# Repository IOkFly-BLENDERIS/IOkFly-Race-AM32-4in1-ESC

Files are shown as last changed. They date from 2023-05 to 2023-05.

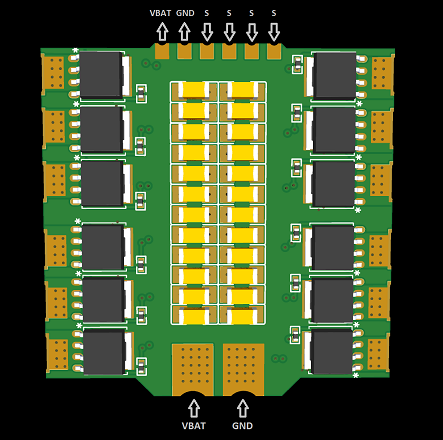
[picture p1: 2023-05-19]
Pictures/ESC pinout.png

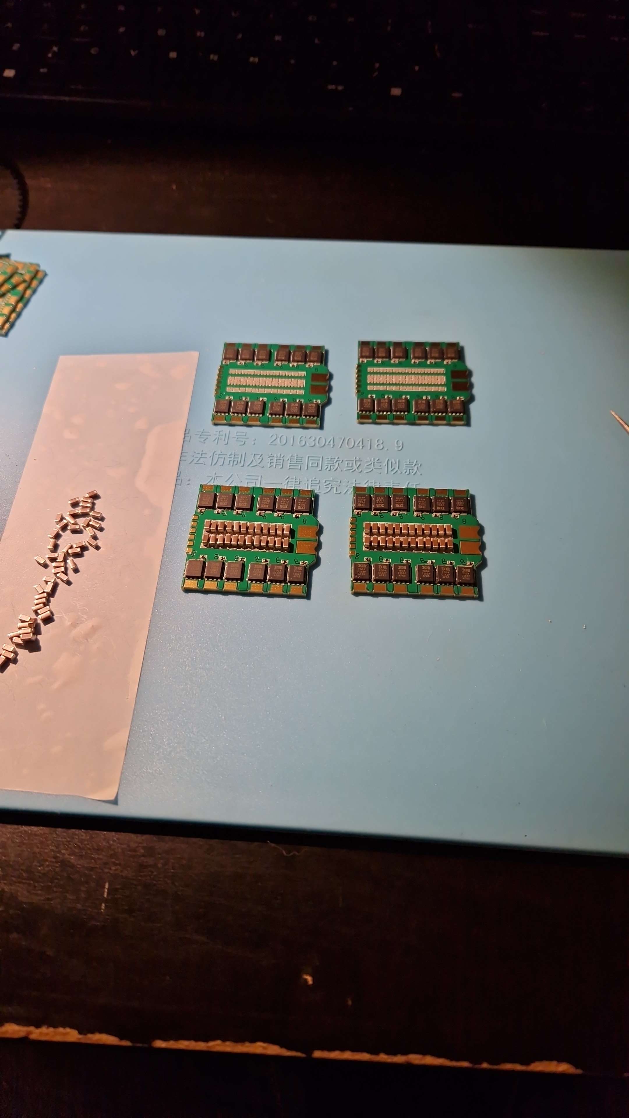
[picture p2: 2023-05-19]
Pictures/X04.jpg

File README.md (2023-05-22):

# IOkFly-Race-AM32-4in1-ESC

<p align="left">
  
</p>

4in1 ESC based on [AM32 FW](https://github.com/AlkaMotors/AM32-MultiRotor-ESC-firmware.git). Every commercial ESC on the market has some sort of design compromise to satisfy as many use cases as possible. My plan was to develop uncompromised, performance oriented ESC for quadcopter racing. Combining all the features mentioned below I believe that I achieved to design a perfect ESC for racing.

# Features

Uses AM32 open sourced 32-bit ESC FW
 * Excellent performance, excellent support and excellent community.

No mounting through holes
 * Allows for optimal mosfet layout to ensure a direct power flow path to each mosfet.
 * Mounting to frames is achieved with 3D printed customizable and replaceable brackets. Top and bottom in any combination of 20x20 or 30.5x30.5 mm.

Split board design
 * Allows to separate all logic components and traces from main power planes for optimal layout of components and somewhat reduces EMI.
 * Reduced heat buildup on sensitive logic components.
 * Allows for uncompromised power plane layers on PDB to achieve excellent power delivery performance.

2 oz copper weight on all 6 layers of power distribution board
 * Improves current flow.
 * Improves heat distribution and heat capacity.
 * Improves shock durability.

High performance Infineon mosfets.
 * In racing power deficit is not an option.
 * [IRFH7004TRPBF](https://www.infineon.com/dgdl/irfh7004pbf.pdf?fileId=5546d462533600a40153561ea3e51ed2)

No current sensor
 * Current sensor and its components use valuable board space and adds a small power flow restriction while in racing it`s almost never used. Best part is no part. There are external XT60 current sensor boards available if needed.\
Ekrānuzņēmums 2023-05-21 213739

FR4 Tg155 board material
 * Higher temperature tolerance and better manufacturing quality.

TDK low ESR filtering caps on the main voltage
 * High quality filtering capacitors reduce noise spikes on main power voltage and increase ESC longevity.

# Specification
 * Voltage: 4-6S
 * Current: 40A < ?
 * MCU - GD32E230G6U6TR
 * Gate driver - FD6288Q
 * Mosfet - IRFH7004TRPBF
 * Target: AM32_SKYSTARS_KM55_E230
 * Mounting: 30.5x30.5 or 20x20 M3 bottoms and 30.5x30.5 or 20x20 tops with M2 or M3
 * Dimensions: 38.1x38.7x12mm
 * Weight: 17g with mount

ESC pinout Processing board

# Manufacturing
I used [EasyEDA](https://easyeda.com/) (free PCB design tool) for designing the boards. [LCS](https://www.lcsc.com/) for ordering components and [JLCPCB](https://jlcpcb.com/) for manufacturing the boards as well as assembling the processing board. Processing board has a lot of 0201 components, and it is almost impossible to assemble in a DIY way.

PCB manufacturing and assembling:

PDB specification: 
 * Layers: 6
 * Base Material: FR4 Tg155
 * PCB Thickness: 1.6mm
 * Inner Copper Weight: 2oz
 * Outer Copper Weight: 2oz
 * Via Covering: Epoxy Filled & Capped
 * Surface Finish: ENIG Gold Thickness:2 U"
 * Castellated Holes: yes, Edges: 4
 
 Processing Board specification:
  * Layers: 6
  * Base Material: FR4 Tg140
  * PCB Thickness: 0.8mm
  * Inner Copper Weight: 0.5oz
  * Outer Copper Weight: 1oz
  * Via Covering: Epoxy Filled & Capped
  * Surface Finish: ENIG Gold Thickness:1 U"
  * Castellated Holes: yes, Edges: 4

For assembling the ESC, I use solder paste with stencil from JLCPCB. Alignment of Processing board on the PCB is critical as the Processing board has very tightly spaced and small castellated holes. Bad alignment may result in shorts or cold soldering. Heat gun soldering or reflow oven will require long and high heat profiles as the PCB has huge thermal capacity. I used cheap soldering heat gun on max temperature settings with medium tip and low air flow for about 5 minutes per side.\
WhatsApp attēls 2023-05-19 plkst 23 57 41 WhatsApp attēls 2023-05-19 plkst 23 58 39

# Mounting

So far, I have used only PETG material for 3D printed mounts. Works well with racing frames such as Switchback. Mounts rigidly to the frame and ESC. Bottom mount requires some sort of threaded inserts to be melted in.
\
Ekrānuzņēmums 2023-05-22 124104

Top mount takes screws directly. Top and bottom part is screwed together with M2 screws in the corners. Recommended height of the frame standoffs are 25mm.

# Testing

Flight testing:
https://www.youtube.com/watch?v=bb6y31JhEbI \
Current draw testing: Coming soon...

# Contributors

Pete Smits\
IOkFly_FluxssFPV\
AM32 Discord community

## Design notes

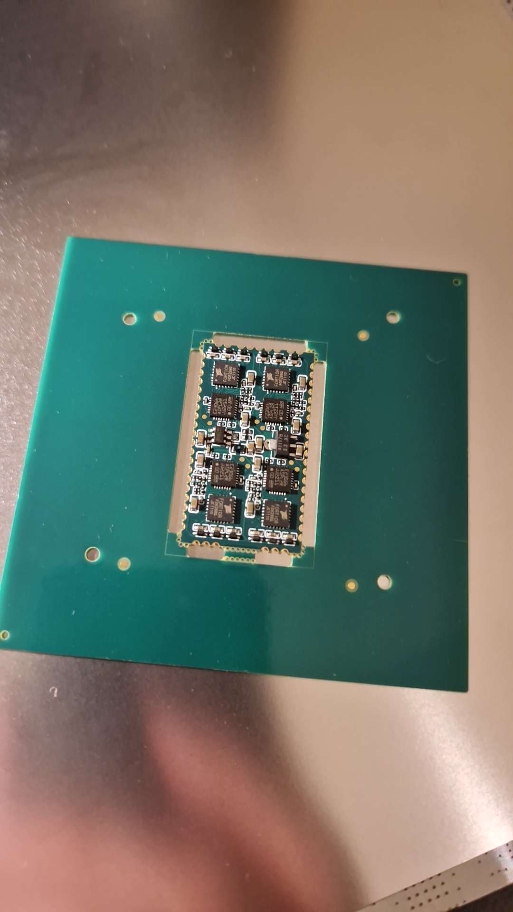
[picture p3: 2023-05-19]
Pictures/X02.jpg

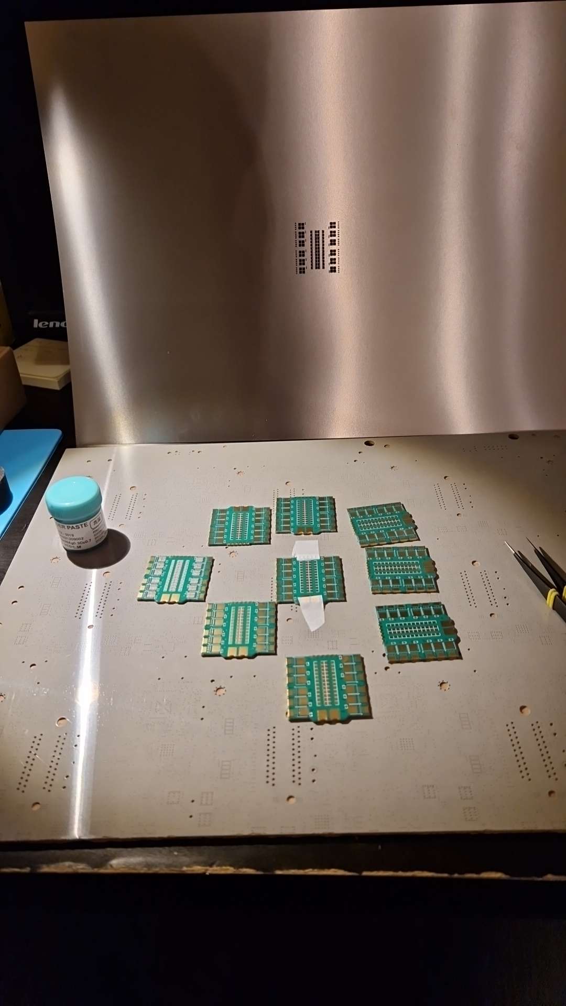
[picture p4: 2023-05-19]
Pictures/X03.jpg

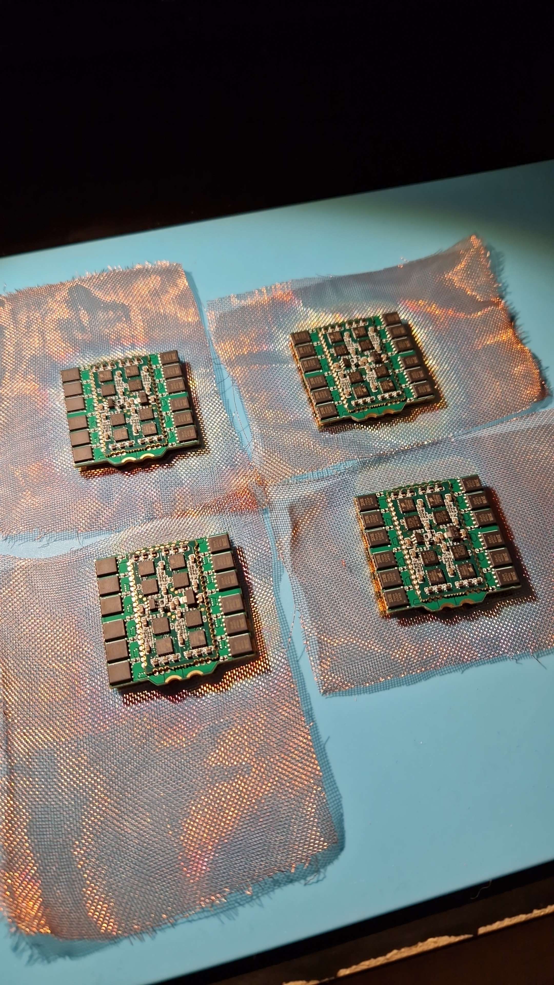
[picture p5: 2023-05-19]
Pictures/X06.jpg

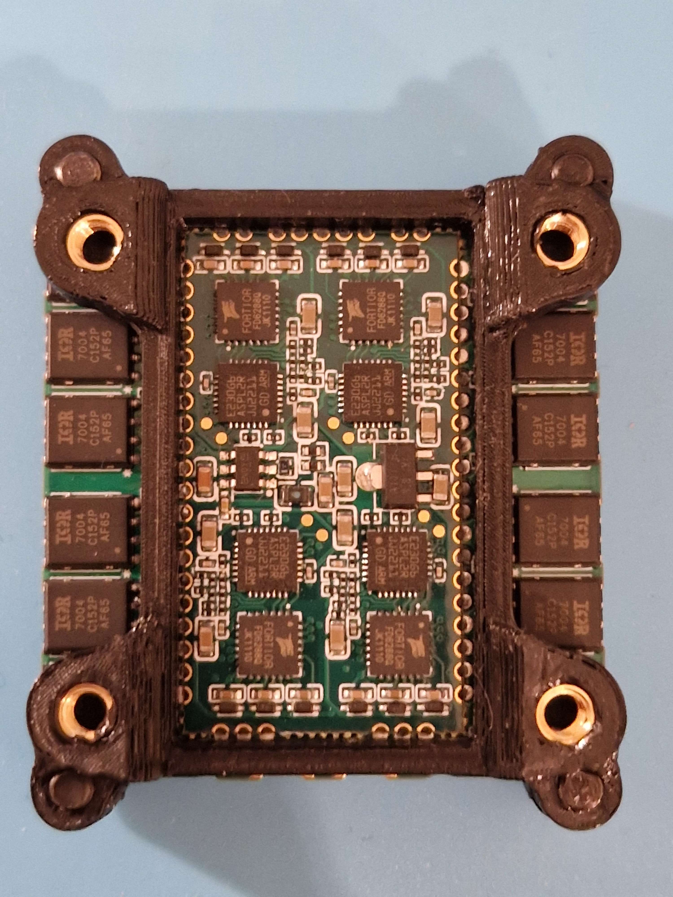
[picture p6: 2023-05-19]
Pictures/X07.jpg

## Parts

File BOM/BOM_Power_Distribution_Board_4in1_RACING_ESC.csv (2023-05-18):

ID | Name | Designator | Footprint | Quantity | Manufacturer Part | Manufacturer | Supplier | Supplier Part | Price
1 | SQJ138ELP-T1_GE3 | U1,U2,U3,U7,U8,U9,U13,U14,U15,U19,U20,U21,U4,U5,U6,U10,U11,U12,U16,U17,U18,U22,U23,U24 | POWERPAK_SO-8L_3_VIS | 24 | IRFH7004TRPBF | Infineon(英飞凌) | LCSC | C112334
2 | 20 | R1,R2,R3,R7,R8,R9,R13,R14,R15,R19,R20,R21,R10,R11,R12,R16,R17,R18,R22,R23,R24,R4,R5,R6 | R0402 | 24 | RC0402FR-0720RL | YAGEO(国巨) | LCSC | C138031 | 0.001
3 | 10uF | C1,C2,C3,C4,C5,C7,C8,C9,C10,C11,C13,C14,C15,C16,C17,C19,C20,C21,C22,C23,C25,C26,C27,C28 | C1206 | 24 | C3216X7R1V106KT000E | TDK | LCSC | C76666 | 0.245

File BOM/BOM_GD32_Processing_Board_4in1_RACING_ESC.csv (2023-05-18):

ID | Name | Designator | Footprint | Quantity | Manufacturer Part | Manufacturer | Supplier | Supplier Part | Price
1 | 1uF | C1,C2,C3,C22,C23,C24,C32,C33,C34,C37,C42,C43 | C0402 | 12 | CL05A105KO5NNNC | SAMSUNG(三星) | LCSC | C29266
2 | 10uF | C4,C9,C20,C30,C40,C45 | C0603 | 6 | CL10A106MO8NQNC | SAMSUNG(三星) | LCSC | C92487 | 0.003
3 | 100nF | C7 | C0402_NEW | 1 | CL05B104KO5NNNC | SAMSUNG(三星) | LCSC | C1525
4 | 4.32K | R52 | R0402 | 1 | RC0402FR-074K32L | YAGEO(国巨) | LCSC | C273329
5 | 1K | R1,R2,R3,R12,R13,R22,R23,R24,R25,R34,R35,R36,R37,R46,R47,R48 | R0201 | 16 | RC0201FR-071KL | YAGEO | LCSC | C138165
6 | 10kΩ | R4,R5,R6,R7,R8,R9,R10,R11,R14,R15,R16,R17,R18,R19,R20,R21,R26,R27,R28,R29,R30,R31,R32,R33,R38,R39,R40,R41,R42,R43,R44,R45 | R0201 | 32 | AR01DTD1002 | Viking Tech | LCSC | C319932 | 0.006
7 | GD32E230G6U6TR | U1,U6,U8,U10 | QFN-28_L4.0-W4.0-P0.40-BL-EP2.8 | 4 | GD32E230G6U6TR | GigaDevice(兆易创新) | LCSC | C2835081 | 0.272
8 | FD6288Q_C328453 | U2,U4,U7,U9 | QFN-24_L4.0-W4.0-P0.50-BL-EP2.6 | 4 | FD6288Q | Fortior Tech | LCSC | C328453 | 0.127
9 | 1N4148WT_C68948 | D1,D2,D3,D4,D5,D6,D7,D8,D9,D10,D11,D12 | SOD-523_L1.2-W0.8-LS1.6-RD | 12 | 1N4148WT T4 | CJ(江苏长电/长晶) | LCSC | C68948 | 0.003
10 | RB161QS-40T18R | D13 | X2-DFN1006-2_L1.0-W0.6-P0.65-RD | 1 | RB161QS-40T18R | ROHM(罗姆) | LCSC | C2837790 | 0.016
11 | 22uH | L1 | IND-SMD_L1.8-W1.2 | 1 | SLC1608F220KTT | Sunltech(韩国顺磁) | LCSC | C411912 | 0.01
12 | 49.9K | R50 | R0402 | 1 | RC0402FR-0749K9L | YAGEO(国巨) | LCSC | C137969
13 | AOZ1282CI | U11 | SOT-23-6_L2.9-W1.6-P0.95-LS2.8-BR | 1 | AOZ1282CI | AOS | LCSC | C111916 | 0.133
14 | CJA1117B-3.3 | U3 | SOT-89-3_L4.5-W2.5-P1.50-LS4.2-BR | 1 | CJA1117B-3.3 | CJ(江苏长电/长晶) | LCSC | C24253 | 0.011
15 | 22uF | C5,C13,C14,C18,C25 | C0603 | 5 | CL10A226MQ8NRNC | SAMSUNG(三星) | LCSC | C59461 | 0.001
16 | 1uF | C6,C12,C17,C27 | C0201 | 4 | CL03A105MO3NRNH | SAMSUNG(三星) | LCSC | C307385 | 0.002
17 | 1uF | C8,C10,C11,C15,C16,C19,C21,C26 | C0201 | 8 | CL03A105MQ3CSNH | SAMSUNG(三星) | LCSC | C53067
18 | 10uF | C28 | C0603 | 1 | GRM188R6YA106MA73D | muRata(村田) | LCSC | C194427 | 0.006

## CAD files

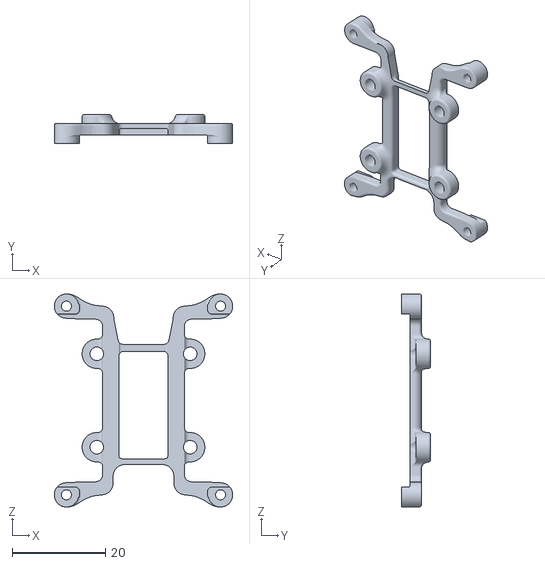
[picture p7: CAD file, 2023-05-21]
Mounting/TOP_20x20_M3.STL
38.2 x 6.30 x 45.6

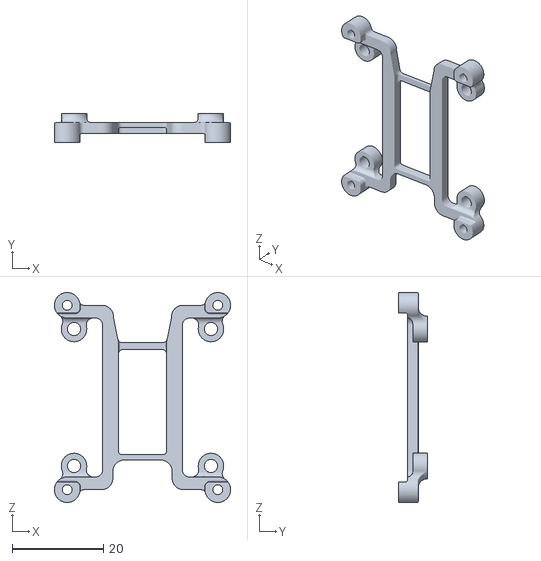
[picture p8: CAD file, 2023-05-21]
Mounting/TOP_30x30_M3.STL
38.6 x 6.30 x 46.0

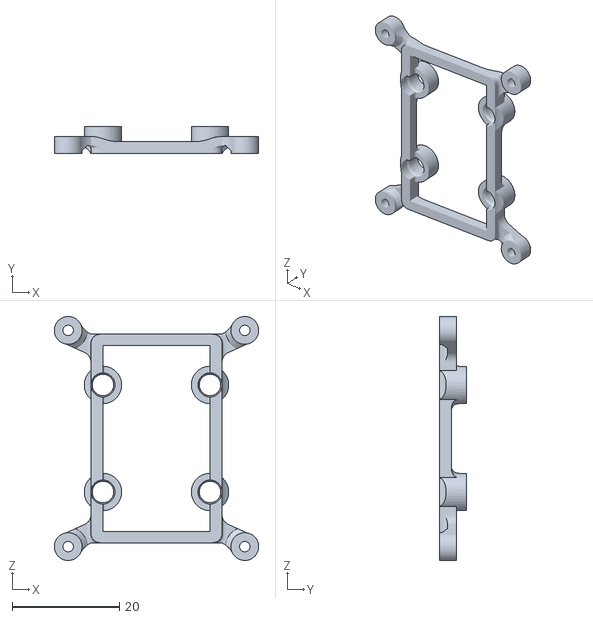
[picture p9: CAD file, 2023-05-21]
Mounting/BOTTOM_20x20_M3_Brass INSERT.STL
38.2 x 5.10 x 45.6

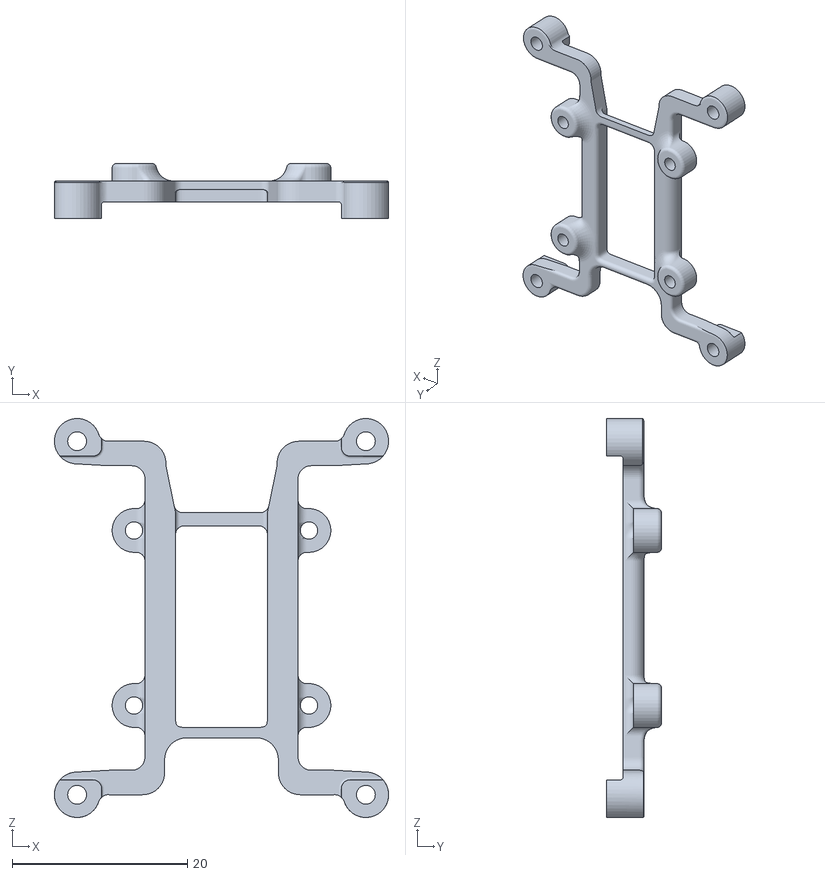
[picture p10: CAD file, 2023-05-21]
Mounting/TOP_20x20_M2.STL
38.2 x 6.30 x 45.6

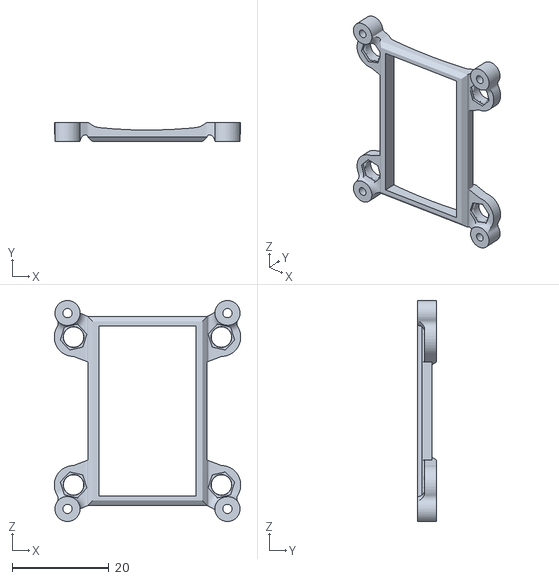
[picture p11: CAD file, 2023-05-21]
Mounting/BOTTOM_30x30_Small M3 INSERTS.STL
38.5 x 4.00 x 45.6

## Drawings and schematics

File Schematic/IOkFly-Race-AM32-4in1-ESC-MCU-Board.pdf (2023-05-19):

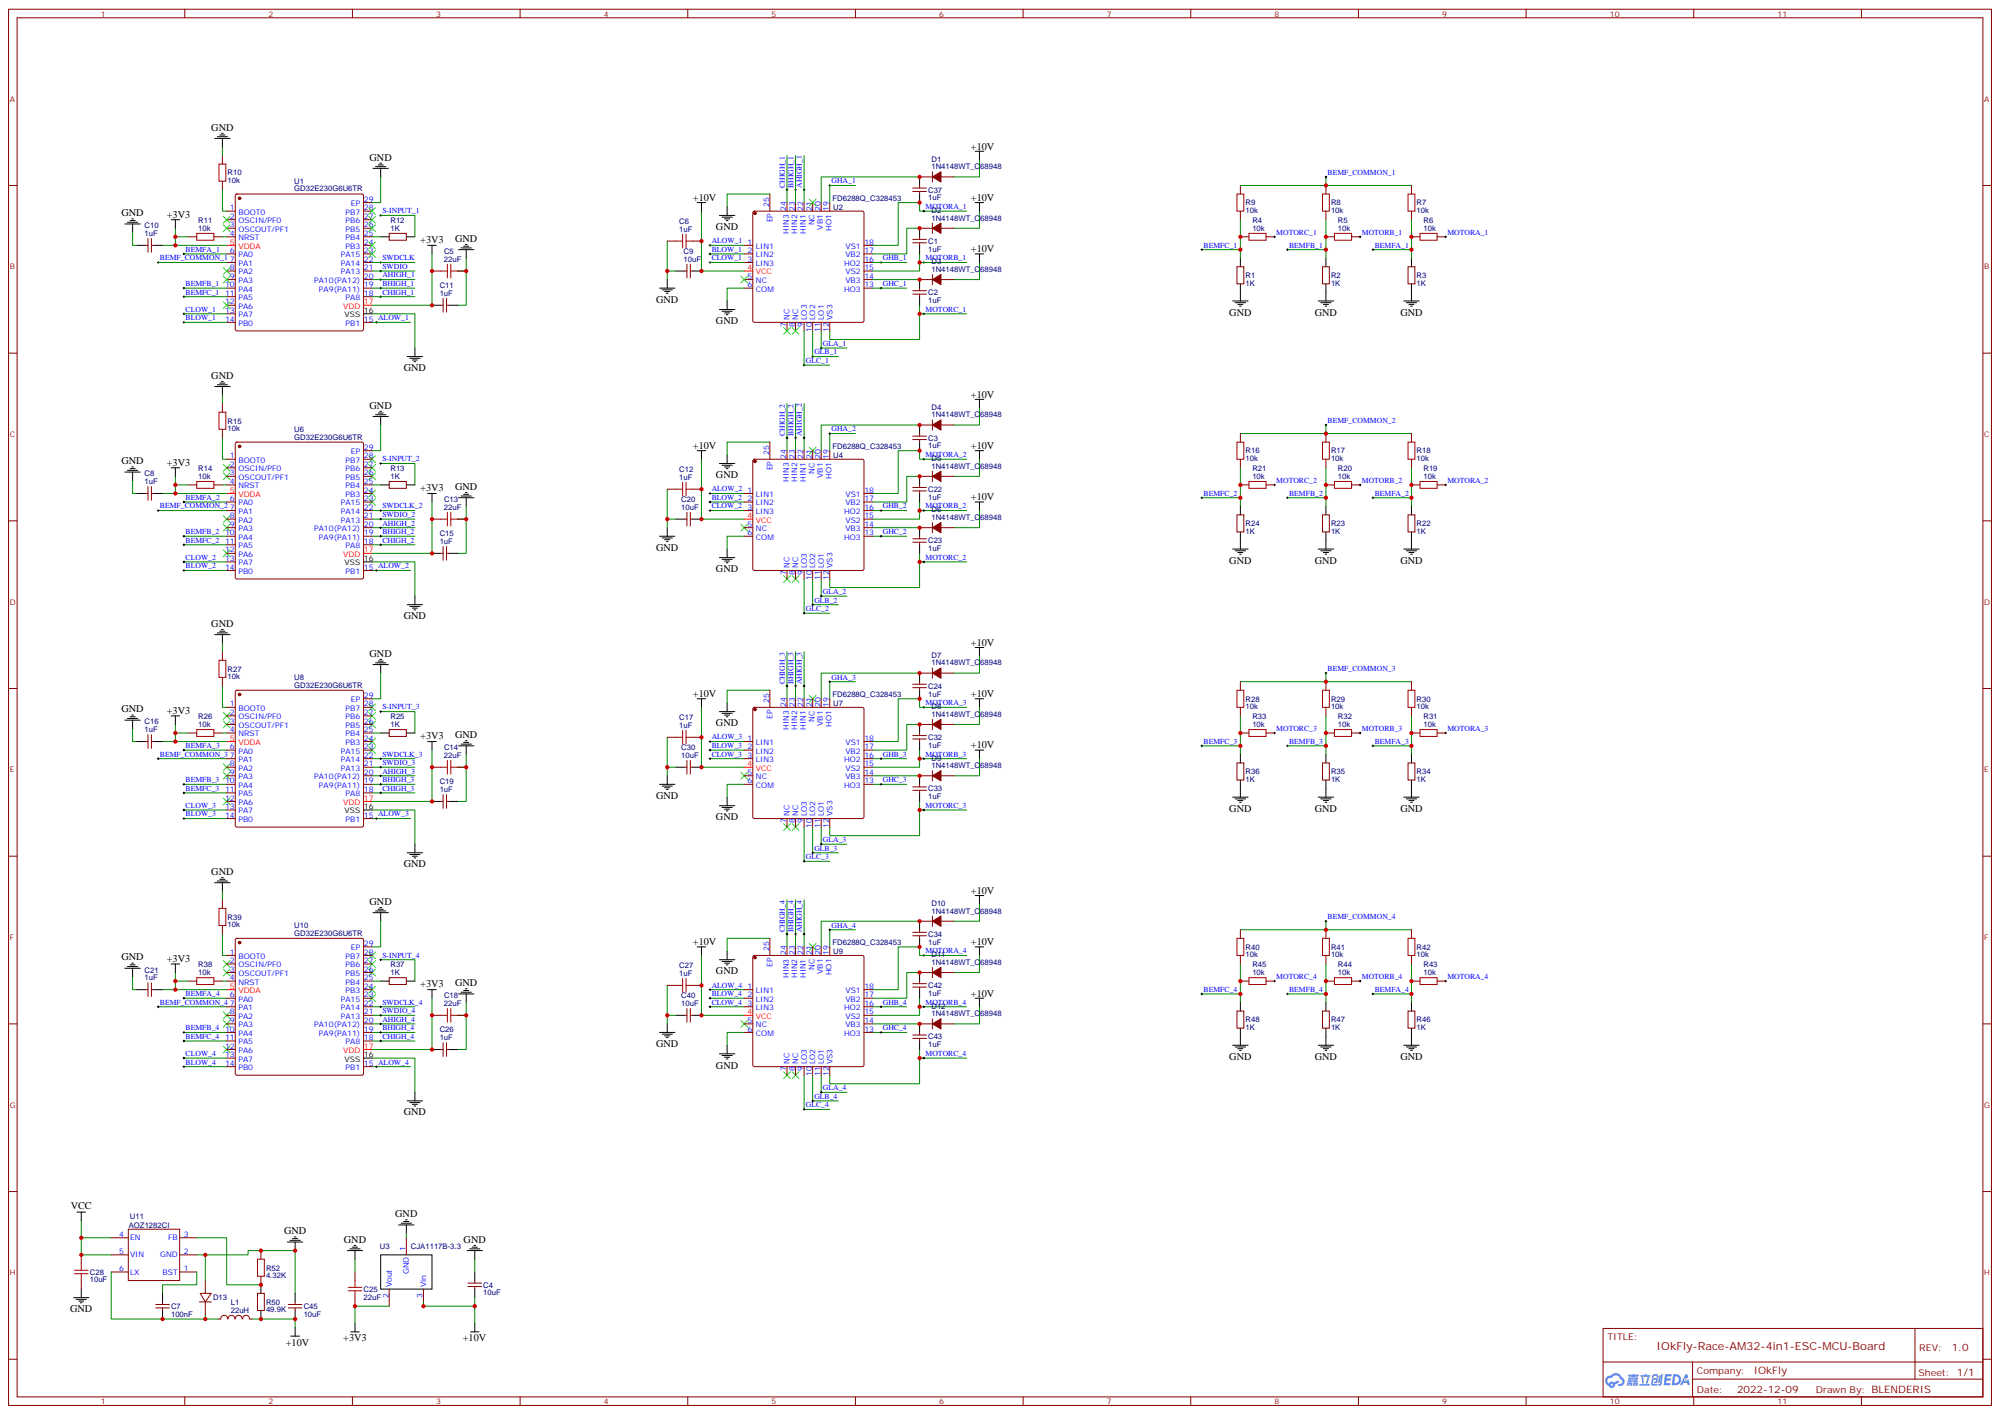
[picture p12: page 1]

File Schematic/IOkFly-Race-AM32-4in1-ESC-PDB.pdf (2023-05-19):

## VCC

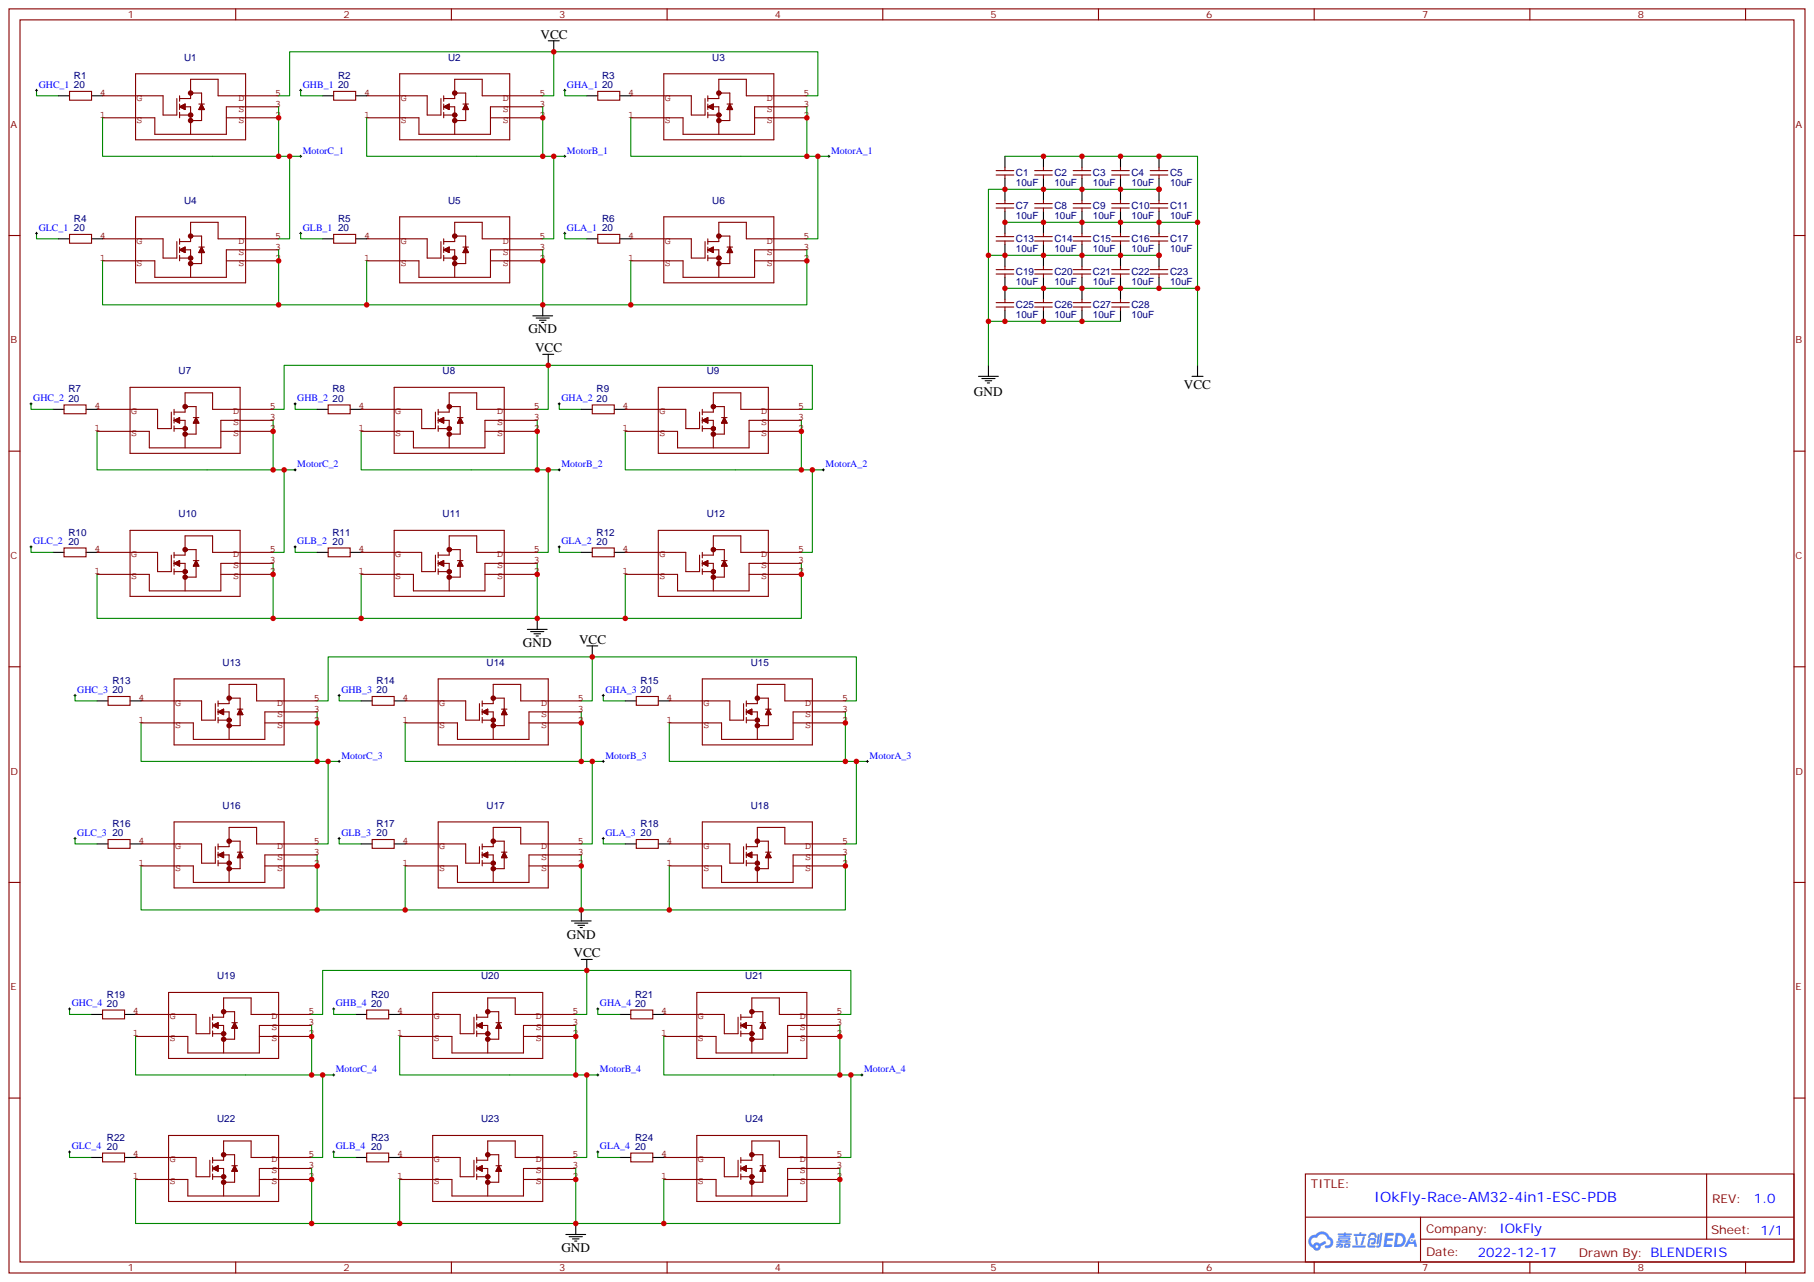
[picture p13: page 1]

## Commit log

2023-05-18 renamed folder
    [Drill_PTH_Through.DRL, Drill_PTH_Through_Via.DRL, Gerber_BoardOutlineLayer.GKO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]
2023-05-18 uploded grabers files to PDB
    [Drill_PTH_Through.DRL, Drill_PTH_Through_Via.DRL, Gerber_BoardOutlineLayer.GKO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]
2023-05-18 BOM File uploads
    [BOM_GD32_Processing_Board_4in1_RACING_ESC.csv, BOM_Power_Distribution_Board_4in1_RACING_ESC.csv]
2023-05-19 Added schematic
2023-05-21 Add of PickAndPlace and Mounting STL
    [BOTTOM_20x20_M3_Brass INSERT.STL, BOTTOM_30x30_Small M3 INSERTS.STL, PickAndPlace_GD32_Processing_Board_4in1_RACING_ESC.csv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]

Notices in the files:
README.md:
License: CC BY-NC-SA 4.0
